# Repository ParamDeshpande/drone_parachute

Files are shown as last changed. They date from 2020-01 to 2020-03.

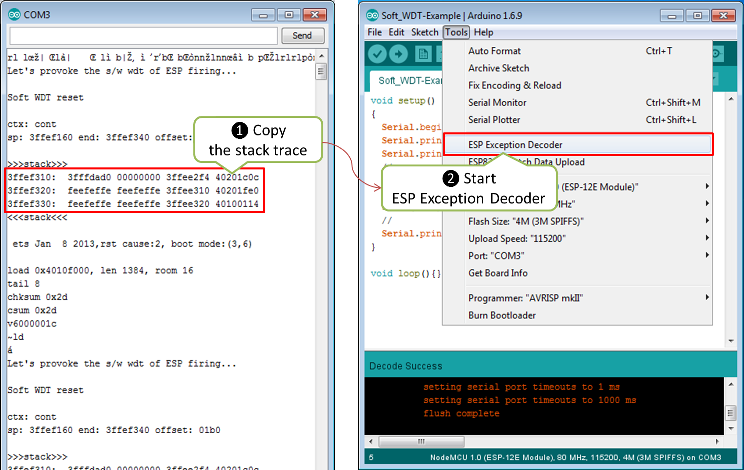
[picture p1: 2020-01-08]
extras/Arduino-master/doc/faq/pictures/a02-decode-stack-tace-1-2.png

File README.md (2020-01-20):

# taxir 
This is the repository for the problem statement 
```
Develop a mechanism (can be software/ hardware/ both ) to deploy a parachute installed on the UAV in case of an emergency landing or power outage. The parachute is placed inside a compartment.
The expected output "Can be in the form of validated electronic circuit design, parachute deployment mechanism, CAD design, code, hardware"
(The code can be written in any programming language of your choice)
```
## Code
There are few versions of the code, please find the latest one in arduino_version. STM_32 mbed version is deprecated has memory overflow issues. 
find the cpp files in /main headers in /include.
 
## Setup

### Mainframe SETUP 

Please do install PlatformIO extension in VSCODE or the arduino IDE, in your pc/laptop depending on which architecture and which is being used or any other if you know what you are doing .... . and do install any HC-05 bluetooth serial terminal. Like [this one](https://play.google.com/store/apps/details?id=de.kai_morich.serial_bluetooth_terminal&hl=en). Or any other as per your preference.

### The system SETUP

Connect the backup battery and main battery in any order whatsover, the system should give an error and should fire the parachute initially cause one of the battery was missing. (new feature or setup init needs to be added here). That way even the end user is assured of the system working.
**HIT THE RESET BUTTON**
Connect your device to get debug via bluetooth, as to what is happening, if everything works out good, you will get debug message on bt stating all's good, else you might find the buzzer still irritating you. And there you go The system is up and ready.

## Conditions 
To eject the parachute, we apply the condition that it must reach a certain speed (1.5 m/s) or more within a specified time interval (0.25 s)
ie an acceleration of about 6m/secsq
. Otherwise, the parachute will not be ejected. Under such conditions, the drone is not allowed to reach a dangerous fall speed.

## Effects ( aka what all is done )
Once the parachute deploys, the system stops the spinning rotors to avoid entanglement with the parachute cords and reduces the risk of laceration injuries to people on the ground.
If battery dies out
relays releases spring support for the chute lid , 
Manual 
Release the flow for the chute aka stop powering the relay to hold the lid
Automatic 
FAILSAFE MECHANISM : The above mentioned in code. 

EITHER WAY OPENS under the given or desired conditions.

## PROTOTYPE GPB VERSION.

SEE  drone_parachute_pcb folder for board schematic.

GPB_image_isometric

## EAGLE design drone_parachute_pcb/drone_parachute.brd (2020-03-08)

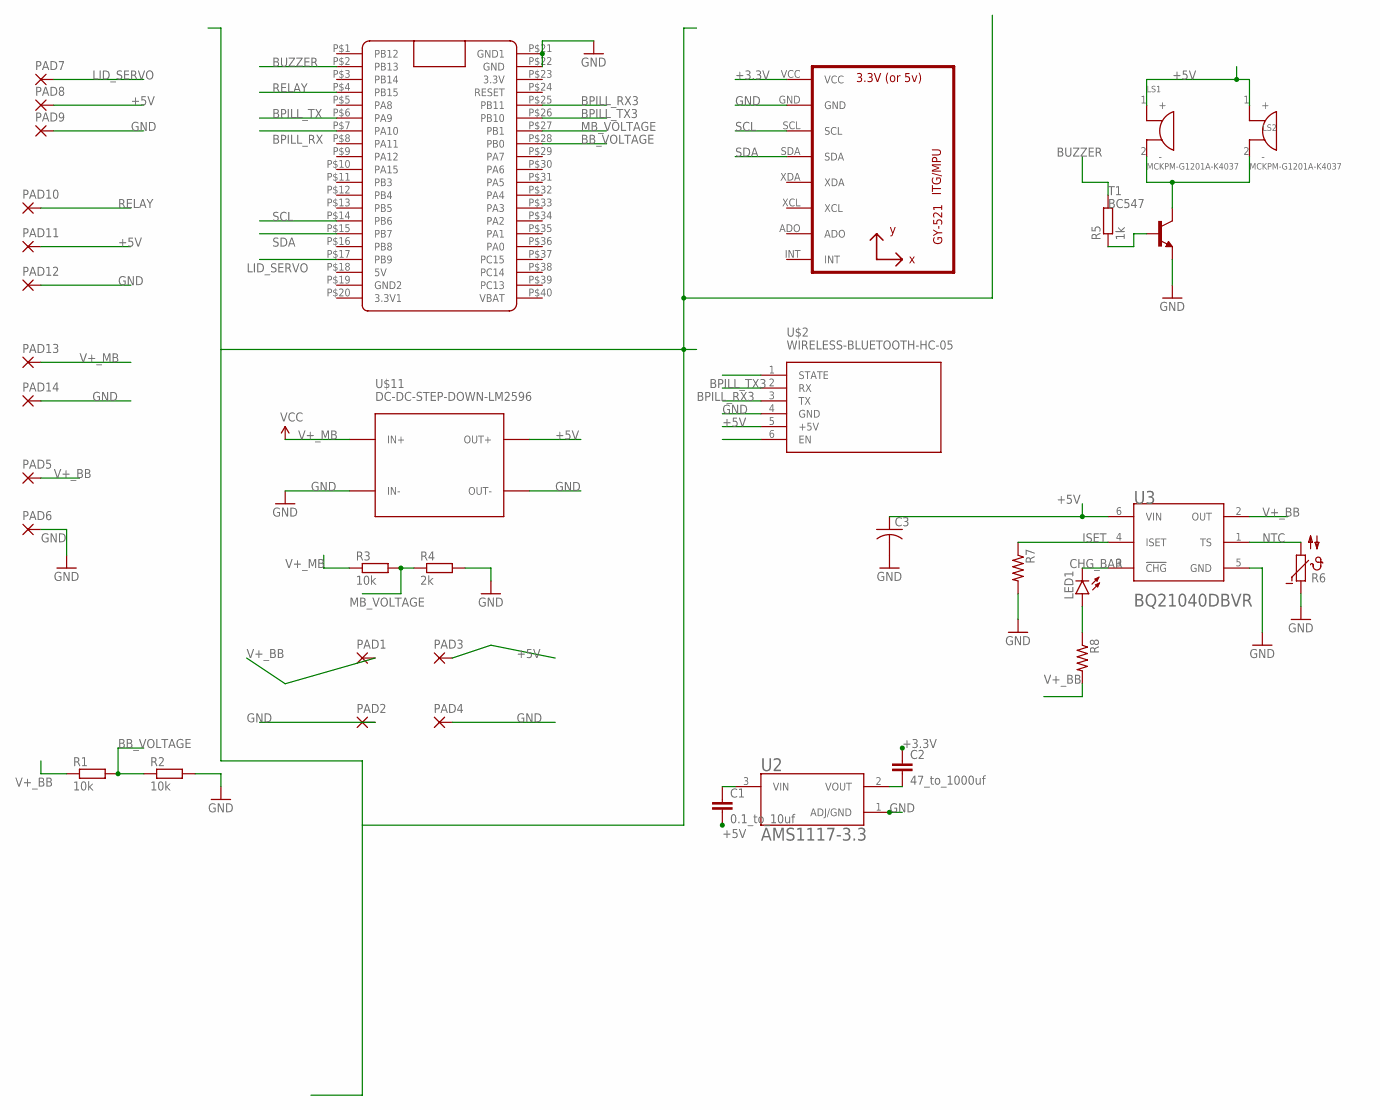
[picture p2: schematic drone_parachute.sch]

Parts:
C1: 0.1_to_10uf; C025-025X050
C2: 47_to_1000uf; C025-025X050
C3: C-USC0805; C0805
LED1: LEDCHIP-LED0805; CHIP-LED0805
LS1, LS2: MCKPM-G1201A-K4037; XDCR_MCKPM-G1201A-K4037
PAD1, PAD2, PAD3, PAD4, PAD5, PAD6, PAD7, PAD8, PAD9, PAD10, PAD11, PAD12, PAD13, PAD14: 1,6/0,8
R1, R2, R3: 10k; 0204/7
R4: 2k; 0204/7
R5: 1k; 0204/7
R6: NTC640; P640
R7, R8: R-US_R0805; R0805
T1: BC547; TO92
U1: GY-521MPU6050; GY-521
U2: AMS1117-3.3; SOT229P700X180-4N
U3: TEXAS_INSTRUMENTS_BQ21040DBVRTEXAS_INSTRUMENTS_BQ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; TEXAS_INSTRUMENTS_BQ21040DBVR_0
U$1: BLUE_PILL
U$2: WIRELESS-BLUETOOTH-HC-05
U$11: DC-DC-STEP-DOWN-LM2596

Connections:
+3.3V: C2.1, U1.VCC
+5V: C1.2, C3.1, LS1.1 (+), LS2.1 (+), PAD3.1, PAD8.1, PAD11.1, U3.6 (VIN), U$2.5 (+5V), U$11.OUT+
BB_VOLTAGE: R1.2, R2.1, U$1.P$28 (PB0)
BPILL_RX: U$1.P$7 (PA10)
BPILL_RX3: U$1.P$25 (PB11), U$2.3 (TX)
BPILL_TX: U$1.P$6 (PA9)
BPILL_TX3: U$1.P$26 (PB10), U$2.2 (RX)
BUZZER: R5.2, U$1.P$2 (PB13)
CHG_BAR: LED1.C, U3.3 (!CHG!)
GND: C3.2, PAD2.1, PAD4.1, PAD6.1, PAD9.1, PAD12.1, PAD14.1, R2.2, R4.2, R6.1, R7.2, T1.1 (E), U1.GND, U2.1 (ADJ/GND), U3.5 (GND), U$1.P$21 (GND1), U$1.P$22 (GND), U$2.4 (GND), U$11.IN-, U$11.OUT-
ISET: R7.1, U3.4 (ISET)
LID_SERVO: PAD7.1, U$1.P$17 (PB9)
MB_VOLTAGE: R3.2, R4.1, U$1.P$27 (PB1)
unnamed: C1.1, U2.3 (VIN)
unnamed: R5.1, T1.2 (B)
unnamed: C2.2, U2.2 (VOUT)
unnamed: LED1.A, R8.1
unnamed: LS1.2 (-), LS2.2 (-), T1.3 (C)
NTC: R6.2, U3.1 (TS)
RELAY: PAD10.1, U$1.P$4 (PB15)
SCL: U1.SCL, U$1.P$14 (PB6)
SDA: U1.SDA, U$1.P$15 (PB7)
V+_BB: PAD1.1, PAD5.1, R1.1, R8.2, U3.2 (OUT)
V+_MB: PAD13.1, R3.1, U$11.IN+

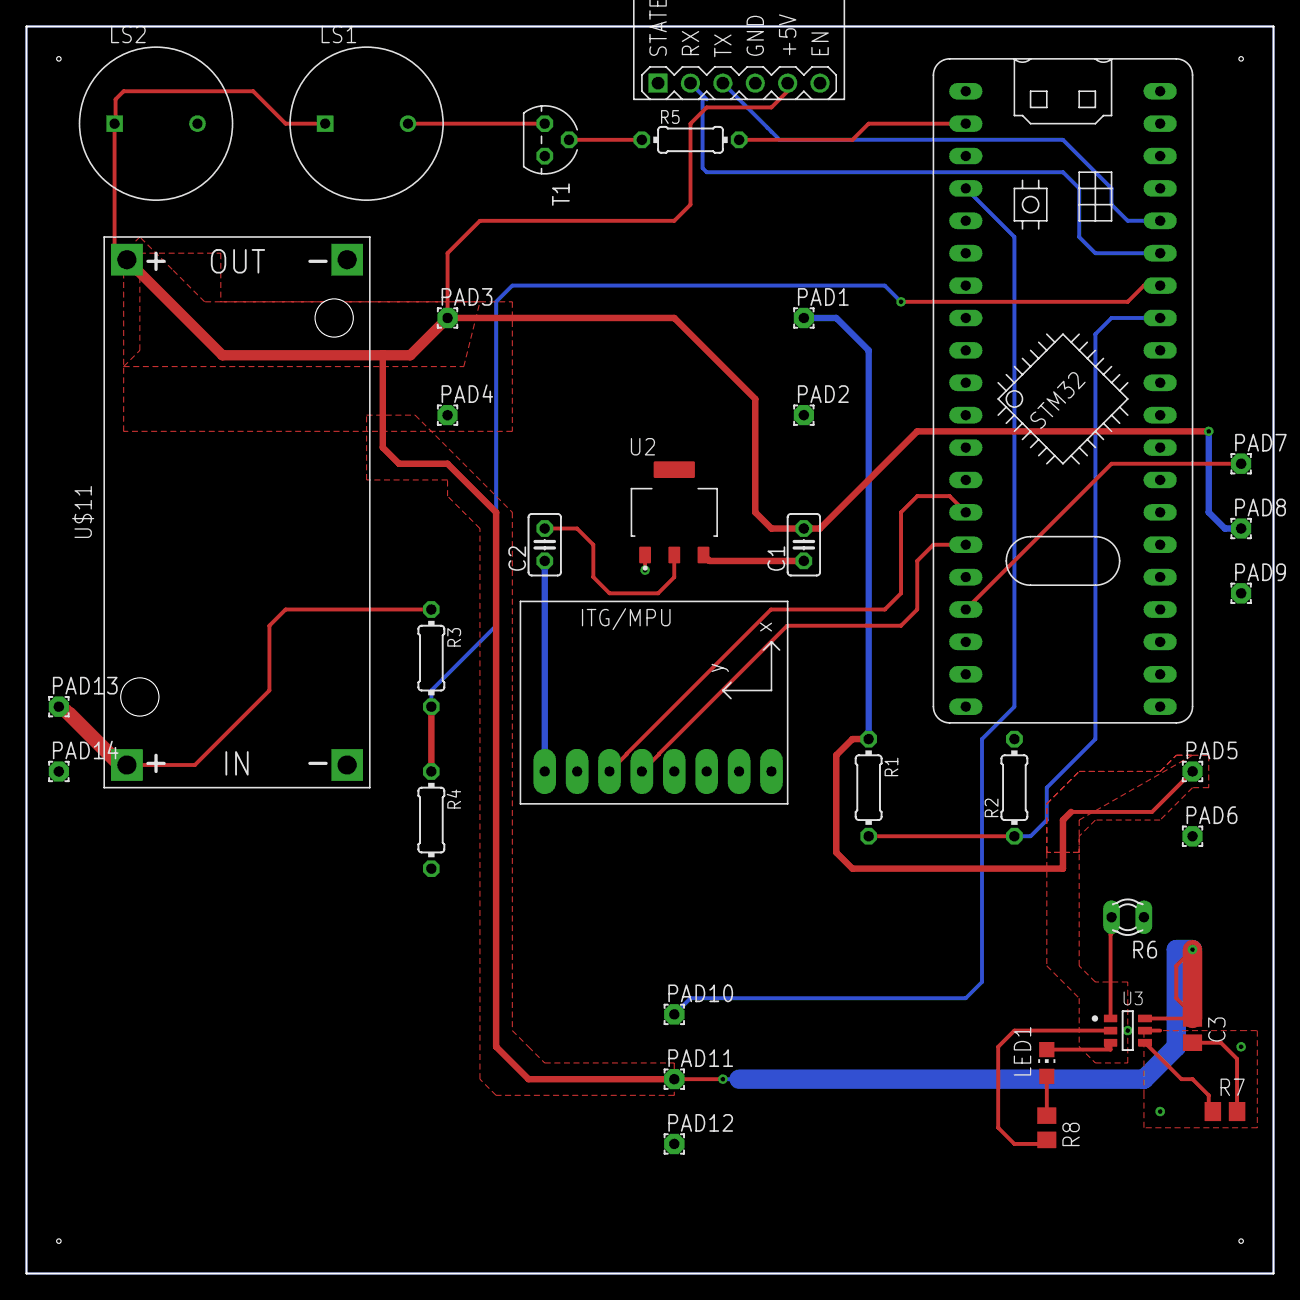
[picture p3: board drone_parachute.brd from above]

Board: 2 copper layers, 97.8 x 97.8 mm, 35 parts (0 on the bottom side), 22 nets.

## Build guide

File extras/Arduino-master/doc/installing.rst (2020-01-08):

Installing
==========

Boards Manager
--------------

This is the suggested installation method for end users.

Prerequisites
~~~~~~~~~~~~~

-  Arduino 1.6.8, get it from `Arduino
   website <https://www.arduino.cc/en/Main/OldSoftwareReleases#previous>`__.
-  Internet connection
-  Python 3 interpreter (Mac/Linux only, Windows installation supplies its own)

Instructions
~~~~~~~~~~~~

-  Start Arduino and open Preferences window.
-  Enter
   ``https://arduino.esp8266.com/stable/package_esp8266com_index.json``
   into *Additional Board Manager URLs* field. You can add multiple
   URLs, separating them with commas.
-  Open Boards Manager from Tools > Board menu and find *esp8266*
   platform.
-  Select the version you need from a drop-down box.
-  Click *install* button.
-  Don't forget to select your ESP8266 board from Tools > Board menu
   after installation.

For more information on the Arduino Board Manager, see:

- https://www.arduino.cc/en/guide/cores

Using git version
-----------------

This is the suggested installation method for contributors and library
developers.

Prerequisites
~~~~~~~~~~~~~

-  Arduino 1.6.8 (or newer, current working version is 1.8.5)
-  git
-  Python 3.x (https://python.org)
-  terminal, console, or command prompt (depending on your OS)
-  Internet connection
-  Uninstalling any core version installed via Board Manager

Instructions - Windows 10
~~~~~~~~~~~~~~~~~~~~~~~~~
- First, make sure you don't already have an ESP8266 core version installed 
  using the Board Manager (see above). If you do, uninstall it from the 
  Board Manager before proceeding. It is also advisable to erase the Arduino15 
  contents.

- Install git for Windows (if not already; see https://git-scm.com/download/win)

-  Open a command prompt (cmd) and go to Arduino default directory. This is typically the
   *sketchbook* directory (usually ``C:\users\{username}\Documents\Arduino`` where the environment variable ``%USERPROFILE%`` usually contains ``C:\users\{username}``)
   
-  Clone this repository into hardware/esp8266com/esp8266 directory.

   .. code:: bash
      
       cd %USERPROFILE%\Documents\Arduino\
       if not exist hardware mkdir hardware
       cd hardware
       if not exist esp8266com mkdir esp8266com
       cd esp8266com
       git clone https://github.com/esp8266/Arduino.git esp8266

   You should end up with the following directory structure in
   
   ``C:\Users\{your username}\Documents\``

   .. code:: bash

       Arduino
       |
       --- libraries
       --- hardware
           |
           --- esp8266com
               |
               --- esp8266
                   |
                   --- bootloaders
                   --- cores
                   --- doc
                   --- libraries
                   --- package
                   --- tests
                   --- tools
                   --- variants
                   --- platform.txt
                   --- programmers.txt
                   --- README.md
                   --- boards.txt
                   --- LICENSE

-  Initialize the submodules

   .. code:: bash

       cd %USERPROFILE%\Documents\Arduino\hardware\esp8266com\esp8266
       git submodule update --init   
  
  If error messages about missing files related to ``SoftwareSerial`` are encountered during the build process, it should be because this step was missed and is required.
  
-  Download binary tools

   .. code:: bash

       cd esp8266/tools
       python3 get.py

-  Restart Arduino

- If using the Arduino IDE for Visual Studio (https://www.visualmicro.com/), be sure to click Tools - Visual Micro - Rescan Toolchains and Libraries 

-  When later updating your local library, goto the esp8266 directory and do a git pull

   .. code:: bash

       cd %USERPROFILE%\Documents\Arduino\hardware\esp8266com\esp8266
       git status
       git pull

Note that you could, in theory install in ``C:\Program Files (x86)\Arduino\hardware`` however this has security implications, not to mention the directory often gets blown away when re-installing Arduino IDE. It does have the benefit (or drawback, depending on your perspective) - of being available to all users on your PC that use Arduino.

Instructions - Other OS
~~~~~~~~~~~~~~~~~~~~~~~

-  First, make sure you don't already have an ESP8266 core version installed 
   using the Board Manager (see above). If you do, uninstall it from the 
   Board Manager before proceeding. It is also advisable to erase the .arduino15 (Linux)
   or Arduino15 (MacOS) contents.

-  Open the console and go to Arduino directory. This can be either your
   *sketchbook* directory (usually ``<Documents>/Arduino``), or the
   directory of Arduino application itself, the choice is up to you.

-  Clone this repository into hardware/esp8266com/esp8266 directory.
   Alternatively, clone it elsewhere and create a symlink, if your OS
   supports them.

   .. code:: bash

       cd hardware
       mkdir esp8266com
       cd esp8266com
       git clone https://github.com/esp8266/Arduino.git esp8266

   You should end up with the following directory structure:

   .. code:: bash

       Arduino
       |
       --- hardware
           |
           --- esp8266com
               |
               --- esp8266
                   |
                   --- bootloaders
                   --- cores
                   --- doc
                   --- libraries
                   --- package
                   --- tests
                   --- tools
                   --- variants
                   --- platform.txt
                   --- programmers.txt
                   --- README.md
                   --- boards.txt
                   --- LICENSE

-  Initialize the submodules

   .. code:: bash

       cd esp8266
       git submodule update --init   
  
  If error messages about missing files related to ``SoftwareSerial`` are encountered during the build process, it should be because this step was missed and is required.

-  Download binary tools

   .. code:: bash

       cd esp8266/tools
       python3 get.py

   If you get an error message stating that python3 is not found, you will need to install it (most modern UNIX-like OSes provide Python 3 as
   part of the default install).  To install you will need to use ``sudo yum install python3``, ``sudo apt install python3``, or ``brew install python3``
   as appropriate.  On the Mac you may get an error message like:

   .. code:: bash

       python3 get.py
       Platform: x86_64-apple-darwin
       Downloading python3-macosx-placeholder.tar.gz
       Traceback (most recent call last):
         File "/Library/Frameworks/Python.framework/Versions/3.7/lib/python3.7/urllib/request.py", line 1317, in do_open
           encode_chunked=req.has_header('Transfer-encoding'))
         ...
         File "/Library/Frameworks/Python.framework/Versions/3.7/lib/python3.7/ssl.py", line 1117, in do_handshake
           self._sslobj.do_handshake()
       ssl.SSLCertVerificationError: [SSL: CERTIFICATE_VERIFY_FAILED] certificate verify failed: unable to get local issuer certificate (_ssl.c:1056)

    This is because Homebrew on the Mac does not always install the required SSL certificates by default.  Install them manually (adjust the Python 3.7 as needed) with:

    .. code:: bash

        cd "/Applications/Python 3.7/" && sudo "./Install Certificates.command"

-  Restart Arduino

-  When later updating your local library, goto the esp8266 directory and do a git pull

   .. code:: bash

       cd hardware\esp8266com\esp8266
       git status
       git pull

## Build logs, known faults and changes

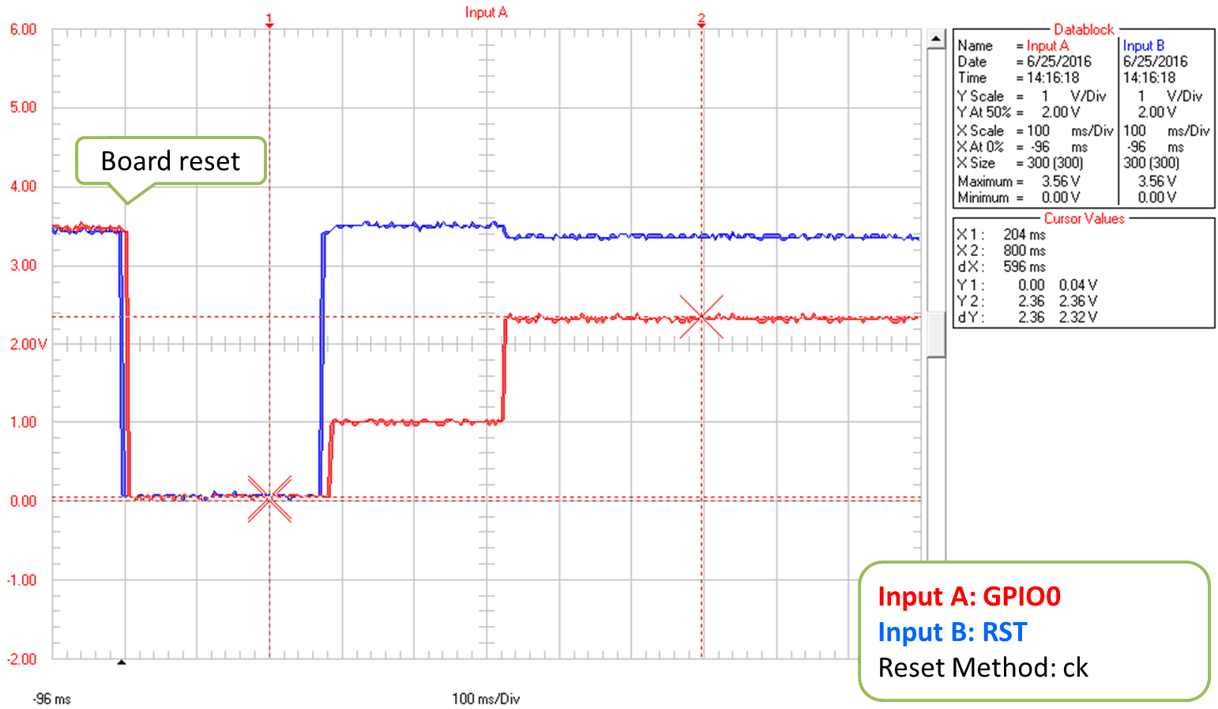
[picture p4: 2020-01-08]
extras/Arduino-master/doc/faq/pictures/a01-reset-ck-closeup.png

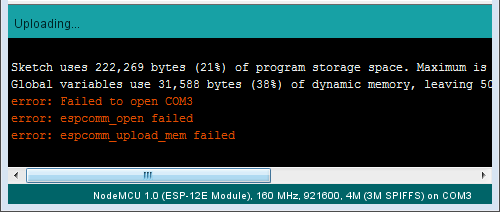
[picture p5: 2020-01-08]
extras/Arduino-master/doc/faq/pictures/a01-espcomm_open-failed.png

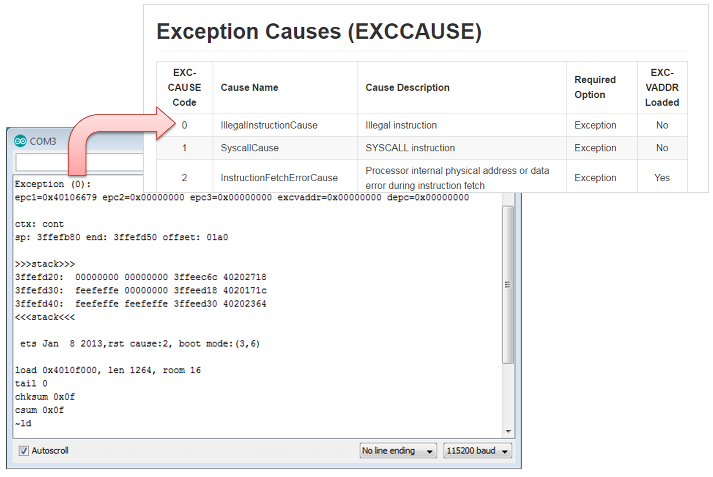
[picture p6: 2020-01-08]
extras/Arduino-master/doc/faq/pictures/a02-exception-cause-decoding.png

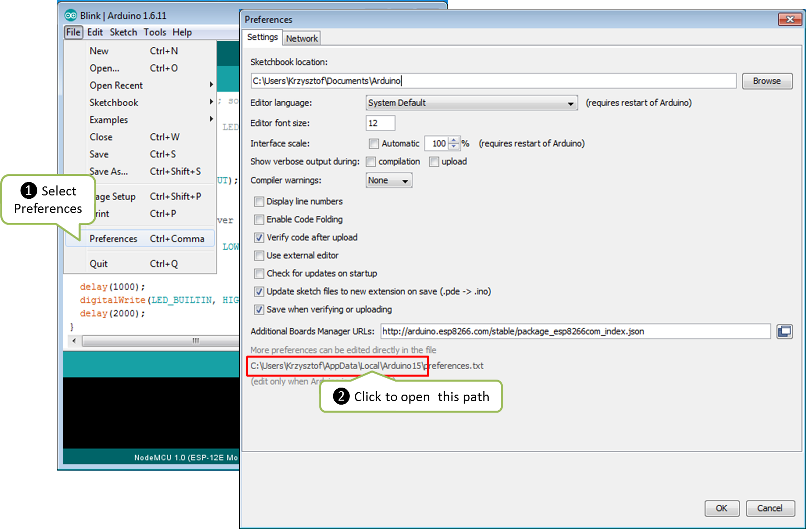
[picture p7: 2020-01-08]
extras/Arduino-master/doc/faq/pictures/a04-arduino-ide-preferences.png

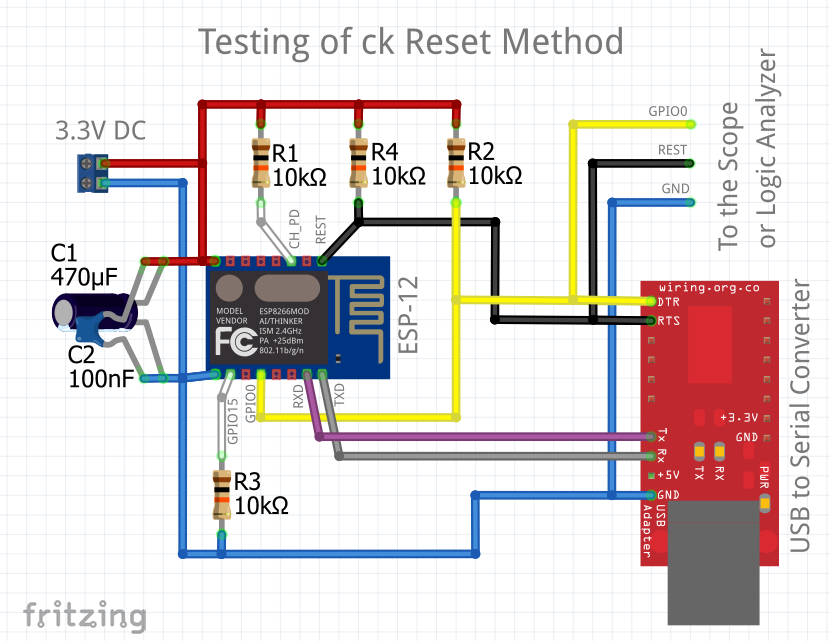
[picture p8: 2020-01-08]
extras/Arduino-master/doc/faq/pictures/a01-circuit-ck-reset.png

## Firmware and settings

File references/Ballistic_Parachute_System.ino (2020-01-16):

/*
Andy Morgan
Auburn REU on SMART UAVs 2016
Research Director: Dr. Richard Chapman

NOTE: Thank you for your interest in the ballistic parachute recovery system. This project was designed as a maker project for open source utilization
on Unmanned Aerial Systems. Please feel free to change the code available in this file. Each chunk of code is commented for easy changes. This code 
could also use different optimizations according to components use. Please change hardcoded thresholds at your discretion for calibration.
Happy Making!
*/




#include <SoftwareSerial.h>
#include <Servo.h> 


//Voltage Sensor Setup
#define MOTOR_CUTOFF_VOLTAGE 9.5 //voltage at which we will claim our battery to be depleted

// GPS Setup
#define rxGPS 2
#define txGPS 3
#define INSIDE_FLIGHT_ZONE_SIZE 20 //this value is in meters and determines how large our flight zone should be

// Accelerometer Thresholds - THIS DEPENDS ON YOUR POWER SOURCE. YOU HAVE TO CHANGE THESE ACCORDINGLY
#define FREE_FALL_LOW_THRESH 310
#define FREE_FALL_HIGH_THRESH 355

//Servo Motor Attachment
#define SERVO_PIN 4

//Relay Attachments
#define RELAY_ON 1  //This will be used to turn relay on (Active Low)
#define RELAY_OFF 0 //Used to turn the relay off
#define RELAY_PIN 5 

//Build Serial Comm to the GPS
SoftwareSerial serialGPS = SoftwareSerial(rxGPS, txGPS);
Servo myservo;
bool AllowToAttach = true; // allow system to attach to servo

//GPS Location Variables
double NLatitude;
double WLongitude;
double StartingNLatitude;
double StartingWLongitude;
double LatitudeThreshold;
double LongitudeThreshold;
String stringGPS = "";
char bufferIn;

// these constants describe the pins.
const int groundpin = A5;             // analog input pin 4 -- ground
const int powerpin = A1;              // analog input pin 1 -- voltage
const int xpin = A2;                  // x-axis of the accelerometer
const int ypin = A3;                  // y-axis
const int zpin = A4;                  // z-axis (only on 3-axis models)
int xval=0; //values obtained through accelerometer
int yval=0;
int zval=0;

//Voltage Read Variables
const int analogInput = A7;           // voltage from the voltage sensor
float vout = 0.0;
float vin = 0.0;
float R1 = 30000.0; //  resistor values inside of the voltage sensor (may need calibrated per sensor)
float R2 = 8250.0; // 
int value = 0;

void setup() {
    //Declare pins for GPS communication
    pinMode(rxGPS, INPUT);
    pinMode(txGPS, OUTPUT);
  
    //Initialize Pins so relays are inactive at reset
    digitalWrite(RELAY_PIN, RELAY_OFF);
  
    //THEN set pins as outputs  
    pinMode(RELAY_PIN, OUTPUT);   
    digitalWrite(RELAY_PIN, RELAY_OFF); //used for redundancy purposes
    
    //Serial Out Setup
    Serial.begin(9600);
    Serial.println("Started");
  
    // GPS Setup
    serialGPS.begin(38400);
    digitalWrite(txGPS,HIGH);
  
    // Attach the needed power to the accelerometer
    pinMode(groundpin, OUTPUT);
    pinMode(powerpin, OUTPUT);
    digitalWrite(groundpin, LOW); //we can do this since our accelerometer does not need much juice. To be more consistent, we can connect ground and power to
    digitalWrite(powerpin, HIGH); //the main 5V and GND from the arduino to keep from calibration. 
  
    //Voltage Sensor Setup
    pinMode(analogInput, INPUT);
  
    // Attach servo pin to the board
    myservo.attach(SERVO_PIN);
    myservo.write(80);  // set servo to closed
    delay(300); // allow it to fully close
    myservo.detach(); 
    //the arduino nano used for this project does not have the computational power to maintain a strict
    //pwm signal and a serial communications signal (for the GPS). We will detach it due to this fact, then reattach later when utilized
  
    //Setup GPS and wait for signal. Calculate Airpsace requirements
    calibrateGPS(); 
  
    //Allow power to the UAV
    digitalWrite(RELAY_PIN, RELAY_ON); //enable UAV to power up
} // end setup

void loop()
{

      getGPSData();
      getAccelValues();
    
    
      //Determine if parachute needs to be deployed... Deployed When:
      // - In free fall
      // - Outside of flight zone
      // - Battery voltage is too low
    if((xval<FREE_FALL_HIGH_THRESH &&xval >FREE_FALL_LOW_THRESH) &&  (yval<FREE_FALL_HIGH_THRESH &&yval >FREE_FALL_LOW_THRESH) && (zval<FREE_FALL_HIGH_THRESH &&zval >FREE_FALL_LOW_THRESH)){ 
               Serial.println("We are in freefall..."); 
               delay(200);
               getAccelValues();
               if((xval<FREE_FALL_HIGH_THRESH &&xval >FREE_FALL_LOW_THRESH) &&  (yval<FREE_FALL_HIGH_THRESH &&yval >FREE_FALL_LOW_THRESH) && (zval<FREE_FALL_HIGH_THRESH &&zval >FREE_FALL_LOW_THRESH))
                     deployParachute();
      }
    
    if((NLatitude > StartingNLatitude+LatitudeThreshold || NLatitude < StartingNLatitude-LatitudeThreshold) || (WLongitude > StartingWLongitude+LongitudeThreshold || WLongitude < StartingWLongitude-LongitudeThreshold)){
               Serial.println("We are outside our airspace..."); 
               deployParachute();
      }
    
    if( getBatteryVoltage() < MOTOR_CUTOFF_VOLTAGE ){
               Serial.println("Battery low..."); 
               deployParachute();  
      }

  
} //end loop

//--------------------------------------------------------------------
//                         Servo Functions
//--------------------------------------------------------------------
//Here we will deploy parachute and cut power to the motors on the drone
void deployParachute(){
   if(AllowToAttach){
        myservo.attach(SERVO_PIN);
        myservo.write(0);  // set servo to open
        digitalWrite(RELAY_PIN, RELAY_OFF); //turn power off to the UAV so that only the backup system is running
        delay(300);
        myservo.detach(); 
        AllowToAttach=false;
      }
}

//--------------------------------------------------------------------
//                    Voltage Sensor Functions
//--------------------------------------------------------------------
//We will determine the current voltage of the battery
float getBatteryVoltage(){
         // read the value at analog input
         value = analogRead(analogInput);
         vout = (value * 5.0) / 1024.0; // see literature on arduino nano
         vin = vout / (R2/(R1+R2)); 
         
         //Serial.print("INPUT V= ");
         //Serial.println(vin,2);
}

//--------------------------------------------------------------------
//                     Acclerometer Functions
//--------------------------------------------------------------------
void getAccelValues(){ // I recommend leaving prints available for calibration
          // print the sensor values:
          xval = analogRead(xpin);
          yval = analogRead(ypin);
          zval = analogRead(zpin);
          Serial.print(xval);
          // print a tab between values:
          Serial.print("\t");
          Serial.print(yval);
          // print a tab between values:
          Serial.print("\t");
          Serial.print(zval);
          
          Serial.println();
}


//--------------------------------------------------------------------
//                          GPS Functions
//--------------------------------------------------------------------

//Check GPS and see if we can grab data. If we can, fill string for use
//There are GPS libraries available, but this requires less overhead for the nano
void getGPSData (){
          // Find dollar sign '$' that will tell us beginning of GPS sequence
         stringGPS = ""; //clear string so that we can append
         if(serialGPS.available()){
            bufferIn = serialGPS.read();
            }
        
        //Grab beginnning sequence from GPS signal    
        if( bufferIn =='$'){
            stringGPS= (String)bufferIn;
            for(int i=0; i<5; i++){
               bufferIn = serialGPS.read();
               stringGPS+= (String)bufferIn;
                }
            }
        
        //We are only going to get data from this sequence beginning. We are not worrying about the othes
        if( stringGPS == "$GPGGA"){
            Serial.println("Sequence: $GPGGA");
            stringGPS = fillGPSString( 74, stringGPS); //size of sequence for $GPGGA is 74 after beginning sequence
            NLatitude = stringGPS.substring(18,27).toFloat(); // This grabs the characters --the last number is the index (0 based +1) - we know this based on form of output
            WLongitude = stringGPS.substring(30,40).toFloat(); // This grabs the characters --the last number is the index (0 based +1)
            Serial.print("Current Coodinates: ");Serial.print(NLatitude); Serial.print("    "); Serial.println(WLongitude);
          }
 
}

// Get data from GPS signal according to the amount of data we need for each sequence
String fillGPSString(int sizeOfSequence, String GPSSequence){
        for(int i=0; i<sizeOfSequence; i++){
               bufferIn = serialGPS.read();
               GPSSequence+= (String)bufferIn;
                }
        return GPSSequence;
}

// Function is called to start our gps coordinate position. This pauses the program until a GPS signal is found and available. 
void calibrateGPS(){
        // Wait for GPS to become available
        while(!serialGPS.available()){
          Serial.println("GPS not available");
          delay (1000);
          }
        Serial.println("GPS available");
        
        
        getGPSData(); 
        while(NLatitude == 0.00 && WLongitude == 0.00){
          getGPSData(); 
          Serial.println("Searching Signal");
        }
        Serial.println("GPS Calibrated");
        //Determine starting coordinates
        
        StartingNLatitude = NLatitude;
        StartingWLongitude = WLongitude;
        LatitudeThreshold = (INSIDE_FLIGHT_ZONE_SIZE/30.79) / 60; //There are 30.79 meters in a Latitude minute, and 60 seconds in a minute
        LongitudeThreshold = (INSIDE_FLIGHT_ZONE_SIZE/24.39) / 60; //There are  meters in a Longitude minute, and 60 seconds in a minute
}

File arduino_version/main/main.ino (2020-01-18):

/*AIM OF MY demo it is show 
1. Buzzers
2. Main battery not present. 
3. Backup battery voltage.
4. all outputs relayed via btooth.
*/

#define DEBUG
#define BT_DEBUG
#ifdef DEBUG_TEST

//#include "port.h"
void setup(){};
void loop(){};
#endif

#ifndef DEBUG_TEST
#include "include/commons.h"
#include "include/battery.h"
#include "include/parachute.h"
#include "include/imu.h"
#include "include/red_pencil.h"
#include "include/executioner.h"

void setup(){
    
    #ifdef DEBUG
    Serial.begin(115200);
    #ifdef BT_DEBUG
    Serial3.begin(9600);
    Serial3.println("can you see me ?");
    #endif
    pinMode(PC13,OUTPUT);
    digitalWrite(PC13,HIGH);
    while(!Serial) {}
    Serial.println("can you see me ?");
    #endif
    error_signal_init();
    #ifdef DEBUG
    Serial.println("err sig init");
    Serial3.println("err sig init");
    
    #endif
    batteries_init();
    #ifdef DEBUG
    Serial.println("batteries_init");
    Serial3.println("batteries_init");
   
    #endif
    parachute_init();
    #ifdef DEBUG
    Serial.println("parachute_init");
    Serial3.println("parachute_init");
    
    #endif
    imu_init();
    #ifdef DEBUG
    Serial.println("imu_init");
    Serial3.println("imu_init");
    
    #endif
    executioner_init();
    #ifdef DEBUG
    Serial.println("executioner init");
    Serial3.println("executioner init");
    
    #endif
    while (true){
        check_system();
    }
    
    /*SHOULD NEVER REACH HERE*/
    while(1);
}

/* SHOULD NEVER REACH HERE*/
void loop(){}; 

#endif
/*END OF FILE */

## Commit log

2020-01-04 blink led code works
2020-01-08 big picture commit
    [a01-circuit-ck-reset.fzz, a01-circuit-nodemcu-reset.fzz, a01-secondary-serial-hookup.fzz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]
2020-01-16 added PCB design.
    [drone_parachute.brd, drone_parachute.sch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]
2020-02-15 added Ti's charging IC details.
2020-02-23 added Ti's charging IC schematic.
    [drone_parachute.brd, drone_parachute.sch]
2020-03-08 added board .brd for charging IC.
    [drone_parachute.brd, drone_parachute.sch]
2020-03-08 reedited all gerber files for newer needs.
    [copper_bottom.gbr, copper_top.gbr, drill_1_16.xln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]

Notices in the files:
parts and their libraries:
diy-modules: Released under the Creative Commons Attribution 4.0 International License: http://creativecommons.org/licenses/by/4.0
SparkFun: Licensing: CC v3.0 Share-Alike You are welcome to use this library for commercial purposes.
